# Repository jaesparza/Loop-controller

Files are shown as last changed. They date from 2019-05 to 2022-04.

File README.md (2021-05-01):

# Loop antenna tunning control <br>

> - High voltage and currents can develop in an efficient loop antenna. If not properly constructed, lethal currents could be derived to your control board.  
> - I make no claims with regards to RF safety, EMC compatibility or compliance to standards of any kind.
> - This is a home-made prototype for hobby applications, you (as potential builder) are solely responsible for your actions.

This project implements a tunning control system for magnetic loop antennas. The antenna is tunned by turning a variable capacitor through a stepper motor at reduced speeds. The controller generates the step signals to be provided to the driver, allows movement only within the specified limits and handles the user interface.

Main characteristics:
- Configurable speeds for fast and slow operation.
- Support for stepper motors of different pulses per rotation and with planetary reductions.
- Smooth stepper motor rotation through microstepping.
- Movement limitation based on discrete step counts or on encoder readings via ADC.

This repository hosts:
- Design calculations
- Hardware designs: schematic, PCB layouts and Gerbers ready to upload for production
- Software implementation of a reconfigurable controller to operate vacuum and butterfly capacitors, with different rotation limit control strategies.
- Notes on mechanical aspects and component selection.

The repository hosts two prototypes: a wired and a wireless control system. As of today only the wired system is complete.

## Wired control - Completed and deployed

| [Software](https://github.com/jaesparza/Loop-controller/tree/master/Software/tunerControllerGen1) | 
[Hardware](https://github.com/jaesparza/Loop-controller/tree/master/pcb/initialPrototype) |

This is a working system relying on a wired connection to deliver motor coil currents as well as reading back the encoder position.

The user interface is implemented through:
- a 16x2 LCD screen to display current capacitor position with a bar and a count,
- two push buttons to trigger clockwise or counter-clockwise rotations,
- a switch to select fast or slow speed.

In my implementation I use an ethernet network cable to be run in parallel with the coaxial cable carrying the RF singal. I have not experienced problems with electrical noise or spurious readings in the ADC due to long cable runs.

## Wireless control - Prototype, on hold
Currently under development, this second version of the controller features wireless control over 802.15.4. The remote control board is intended to be placed together with the antenna in the remote location. The user interacts with the control through a PC application.

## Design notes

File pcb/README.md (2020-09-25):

# Hardware notes

Fixes:

* **Pull-up fix in the enable motor stepper controller signal**  it is important to add a 1 kOhm pull-up to the enable signal so it has a defined state when the microcontroller is going through a power-on/reset. It can be added easily on the back of the PCB between the *Enable* and the *Vcc* pins.

## Wired control board
- Only revB of the PCB is available in here, revA had routing problems and was discarded in the design tool.
- The hardware was developed with easyEDA and I used JLPCB for production.

## Wireless control board
- The hardware was developed with KiCAD and I used JLPCB for production.

Misc. notes:
- Power through LiPo battery - solar panel could be used.
- The control board runs at 3V to reduce power consumption and to avoid level shifters to interface peripherals. Software is currently under development.

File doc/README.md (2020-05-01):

# Documentation

## Datasheets
Due to copyright I do not upload datasheets to GitHub, but I do keep a list of links to the original sources so it is easy to find information.
* Stepper motor driver Allegro A4988 - [Link to datasheet](https://www.pololu.com/file/0J450/a4988_DMOS_microstepping_driver_with_translator.pdf)
* Microcontroller ATmega 328p - [Link to datahseet](http://ww1.microchip.com/downloads/en/DeviceDoc/Atmel-7810-Automotive-Microcontrollers-ATmega328P_Datasheet.pdf)
* Microcontroller ATmega32U5 - [Link to datasheet](http://ww1.microchip.com/downloads/en/DeviceDoc/Atmel-7766-8-bit-AVR-ATmega16U4-32U4_Summary.pdf)
* FTDI cable pinout - [Link to manual](https://www.ftdichip.com/Support/Documents/DataSheets/Cables/DS_TTL-232R_CABLES.pdf)
* Stepper motor with planetary reduction 5:1 - 17HS15-1684S-PG5 -[Link to datasheet](https://www.omc-stepperonline.com/download/17HS15-1684S-PG5.pdf)
* Stepper motor 400 rev - 42BYGHM809 - Available in this repository

## Schematics
* Arduino pro mini - Available in this repository - License Attribution Share-Alike 3.0
* Arduino pro micro - Available in this repository - License Attribution Share-Alike 4.0
* A4988 breakout board [Link to schematic](https://a.pololu-files.com/picture/0J3359.600.jpg?bafae85a9d4ff4a7837ec16a322748fe)
* Minimal circuit needed to drive the stepper in a test setup [Link to schematic](https://a.pololu-files.com/picture/0J10073.600.jpg?75d9ca5bb2e095e5c5f64350019e1b81)

## Others
* Mechaduino [hardware](https://github.com/jcchurch13/Mechaduino-Hardware) and [firmware](https://github.com/jcchurch13/Mechaduino-Firmware) git repositories.

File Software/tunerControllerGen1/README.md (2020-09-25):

# Tuner controller - Generation 1
This is the firmare for the first generation control board. It has been developed using CPP and parts of the Arduino framework as Hardware Abstraction Layer (HAL). 

Main features are:
* The firmware can be configured to control different kinds stepper motors at different speeds.
* The LCD position bar can be recalibrated to represent approximate capacitance graphically between min and max values.
* The LCD refresh rate can be reconfigured so it does not affect motor operation.
* Capacitor position is stored in EEPROM and therefore is persistent accross reboots.
* The firmare is easily portable to other architectures by changing the hw dependand class implementations (`Input.cpp`, `StepperMotor.cpp`, `UI.cpp` and `EepromAccess.h`).

## Operation

* Select speed by toggling the speed switch between SLOW or FAST.
* Move the capacitor in the desired direction by pushing CW or CCW. Progress bar and rotation count are incremented during movement and immediately upon pushbutton release.
* To clear EEPROM contents and set the position count to 0:
  1. Push reset button.
  2. Push both CW and CCW buttons at the same time.
  3. Release the reset button while keeping CW and CCW pushed.
  4. Release CW and CCW
  5. Board will boot and set the position to 0.

## Software structure
The control software is structured as depicted below. Comments after `##`

```bash
tunerControlGen1/
|── tunnerControllerGen1.ino                ## Initialization and entry point
├── HardwareConfig.h                        ## Configuration of hardware connections and motor timing
├── src/                                    
│   ├── lib                                 ## Third party library for faster LCD interfacing (no blocking)
|   |   ├── LiquidCrystalFast.h
|   |   └── LiquidCrystalFast.cpp
│   ├── modes                               ## Operational modes
|   |   ├── Mode.h
|   |   ├── ModeCalibrate.h
|   |   └── ModeOperate.h
│   ├── hwControl                           ## Hardware dependant class definitions and implementations for Arduino
|   |   ├── characterDefinitions.h
|   |   ├── UI.h
|   |   ├── UI.cpp
|   |   ├── StepperMotor.h
|   |   ├── StepperMotor.cpp
|   |   ├── EepromAccess.h
|   |   ├── Input.h
|   |   └── Input.cpp
|   └── 
└── 
```

## How to configure the firmware

The firmaware can be configured to drive motors at different speeds by altering the timing parameters in the table below. Additionally, care must be taken so the update of the LCD does not interfere the driver pulsing to a point in which it affects smooth movement. This can be controlled by modifying the number of pulses required to trigger a display update. 

| Parameter name | Description | Unit |
|---| ---|---|
| DELAY_SLOW | Pulse duration for slow operation. | microseconds | 
| DELAY_FAST | Pulse duration for fast operation. | microseconds | 
| OPERATION_DELAY_SLOW  | Delay between pulses in slow mode.| milliseconds |
| OPERATION_DELAY_FAST  | Delay between pulses in fast mode.| milliseconds | 
| DECIMATE | Division factor applied to the steps count printed on the LCD | N/A - discrete count|
| MAX_COUNT | Maximum number of counts for a full progress bar. | steps | 
| REFRESH_INTERVAL | Number of pulses needed to trigger a LCD update. | N/A - discrete count  |
| SOFT_LIMIT_MIN | Minimum stepper count. Steps will not be sent below this limit (CW steps).| steps |
| SOFT_LIMIT_MAX | Maximum stepper count. Steps will not be sent above this limit (CCW steps).| steps|
| ENCODER_MIN || raw adc counts|
| ENCODER_MAX || raw adc counts|

These parameters can be set in the file `HardwareConfig.h` by activating the relevant configuration via `#define CONF_#` or writing an additional one. Extract of HardwareConfig, with `CONF_1` as active configuration below.

```C
#define CONF_1

#ifdef CONF_1
/* Configuration for a stepper motor of 400 pulses per revolution, no planetary
 * reduction built-in.
 *
 *  This motor is intented to be used with a butterfly capacitor. This capacitor
 * type goes from minimum capacity to maximum with a 90 deg rotation = 1/4 of a
 * full rotation. Coupling to the capacitor is directly to the shaft (no
 * additional mechanical reduction).
 *
 *  Microswitches configured for maximum microstepping for minimum vibrations.
 *  switches 1 - LOW
 *           2 - LOW
 *           3 - LOW
 */
#define REFRESH_INTERVAL     50
#define DELAY_SLOW           300
#define DELAY_FAST           100
#define MAX_COUNT            1600
#define DECIMATE             1
#define OPERATION_DELAY_SLOW 50
#define OPERATION_DELAY_FAST 10
#define SOFT_LIMIT_MIN       0
#define SOFT_LIMIT_MAX       1600
#endif // CONF_1
```

In addition to the parameters from above, microstepping in the stepper driver is recommended for smoother operation. This firmware interfaces the A4988 driver, that supports the following microstepping options:

| MS1 | MS2 | MS3 | Microstep |
|-----|-----|-----|---|
| L | L | L | Full step |
| H | L | L | 1/2  step |
| L | H | L | 1/4 step  |
| H | H | L | 1/8 step  |
| H | H | H | 1/16 step |

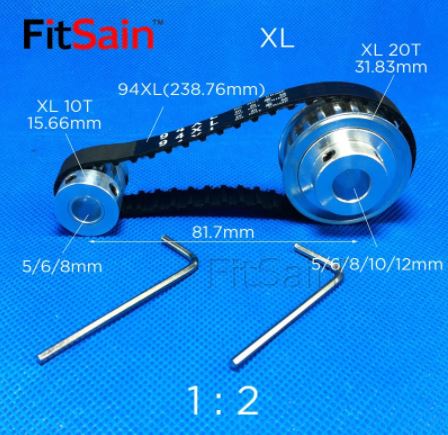
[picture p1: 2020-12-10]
doc/images/tansmission.JPG

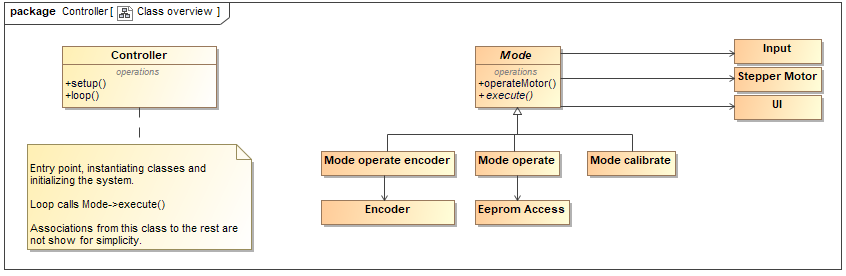
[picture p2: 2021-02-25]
doc/images/controllerStructure.PNG

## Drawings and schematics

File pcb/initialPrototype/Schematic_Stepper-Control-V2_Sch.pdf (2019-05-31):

## VCC VCC

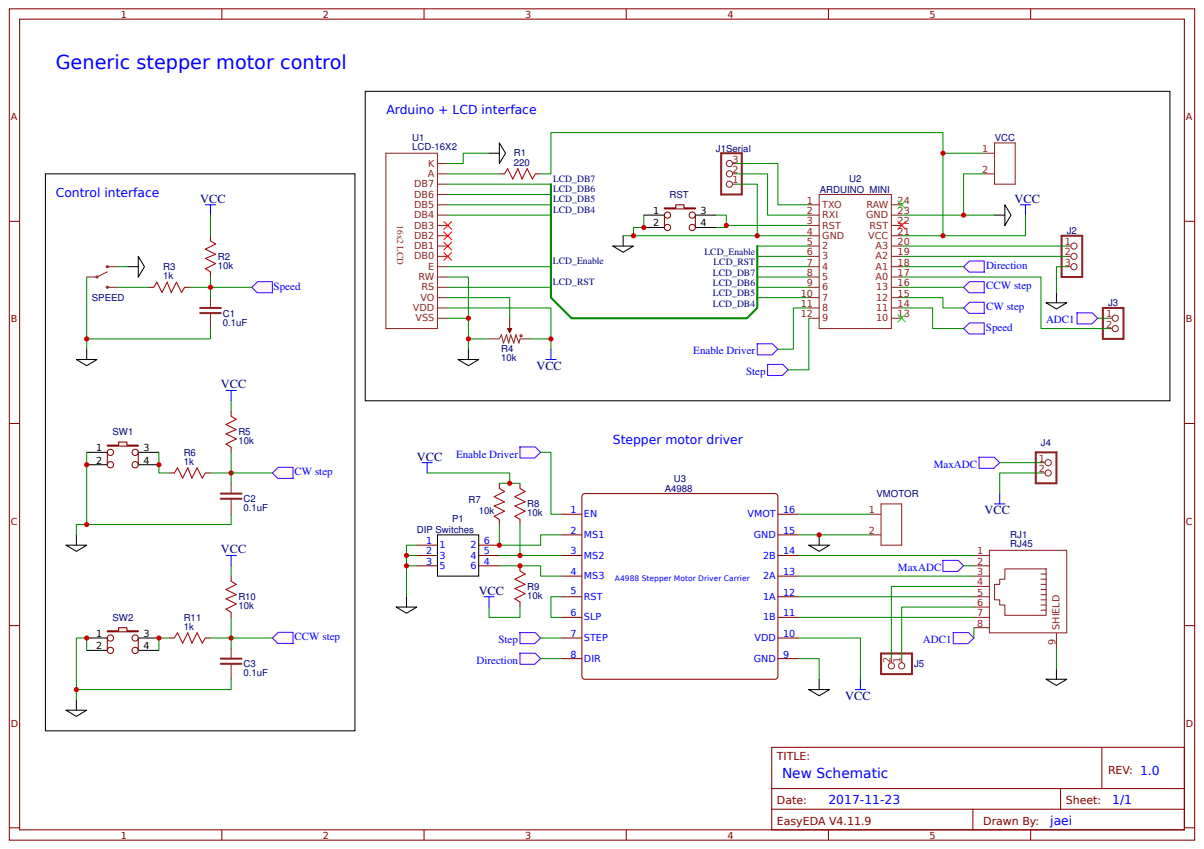
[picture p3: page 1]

Generic stepper motor control

A4988 Stepper Motor Driver Carrier

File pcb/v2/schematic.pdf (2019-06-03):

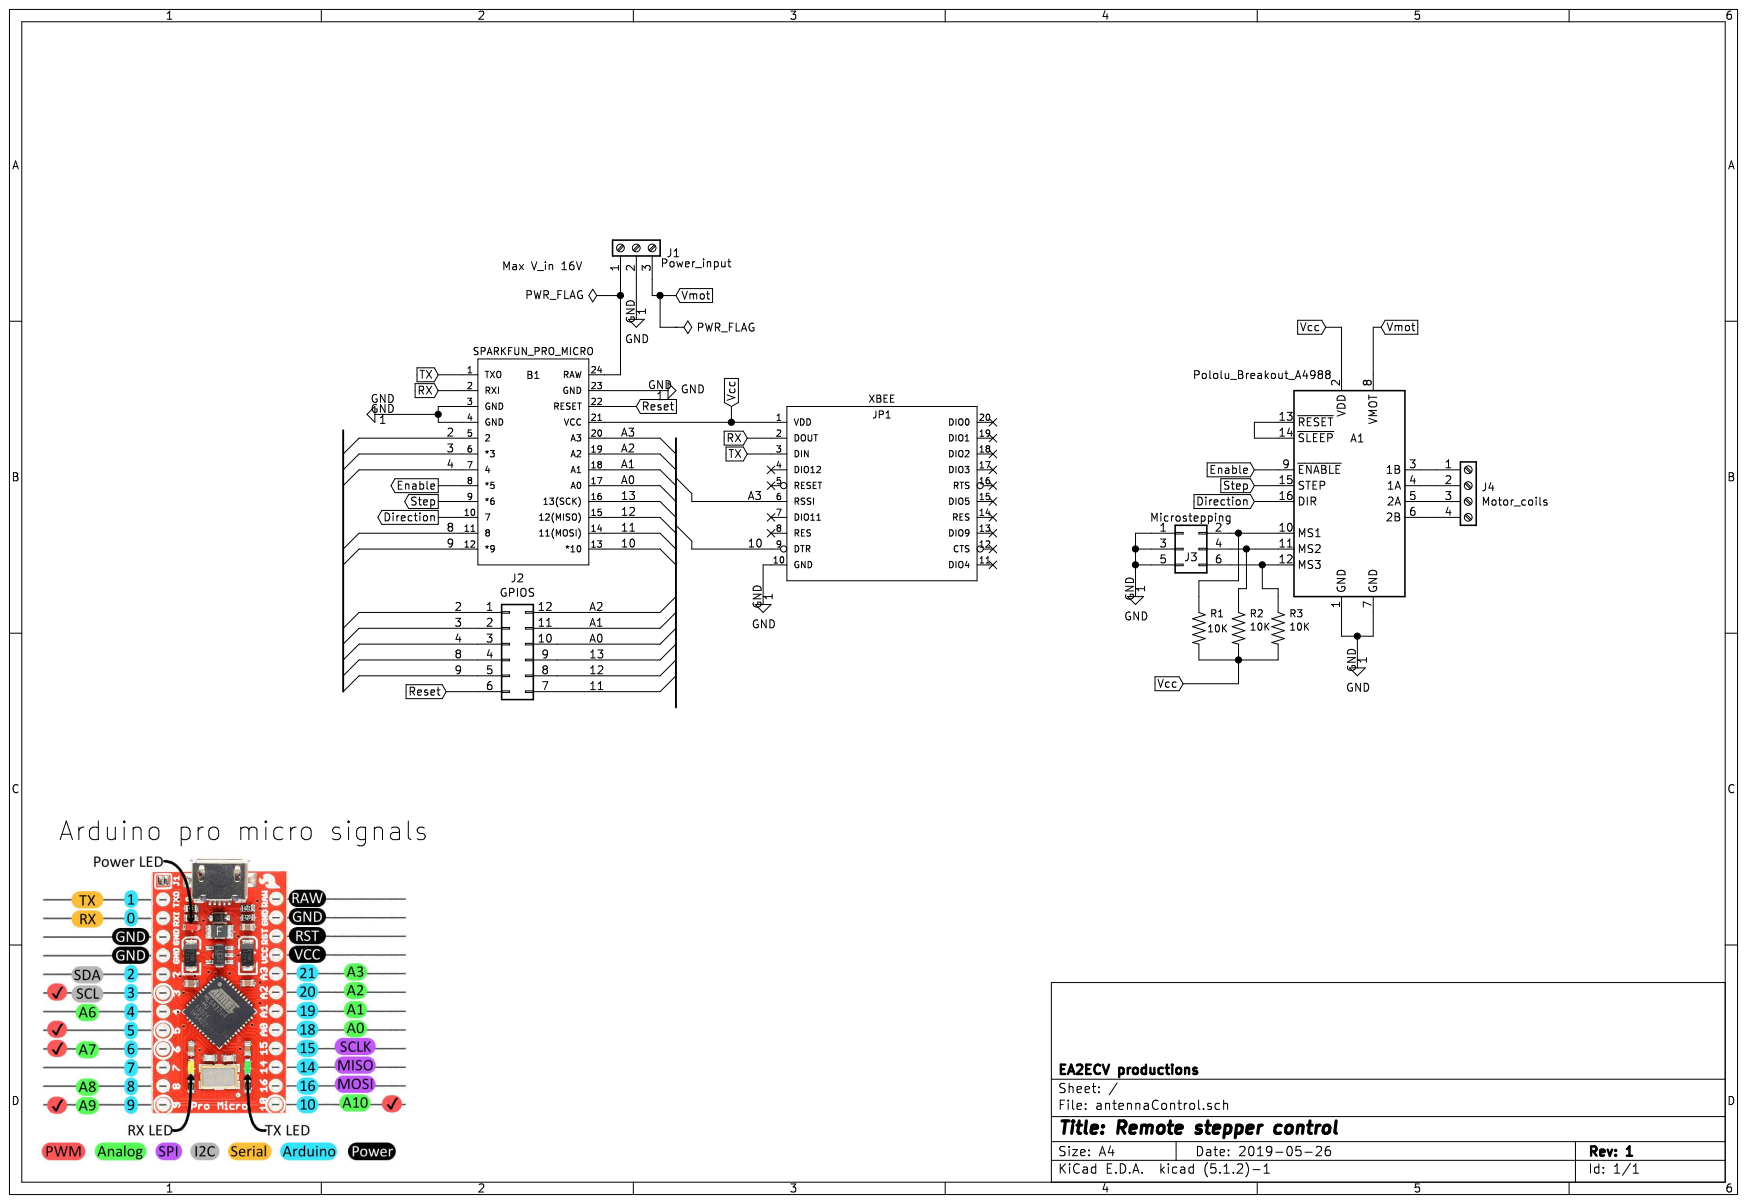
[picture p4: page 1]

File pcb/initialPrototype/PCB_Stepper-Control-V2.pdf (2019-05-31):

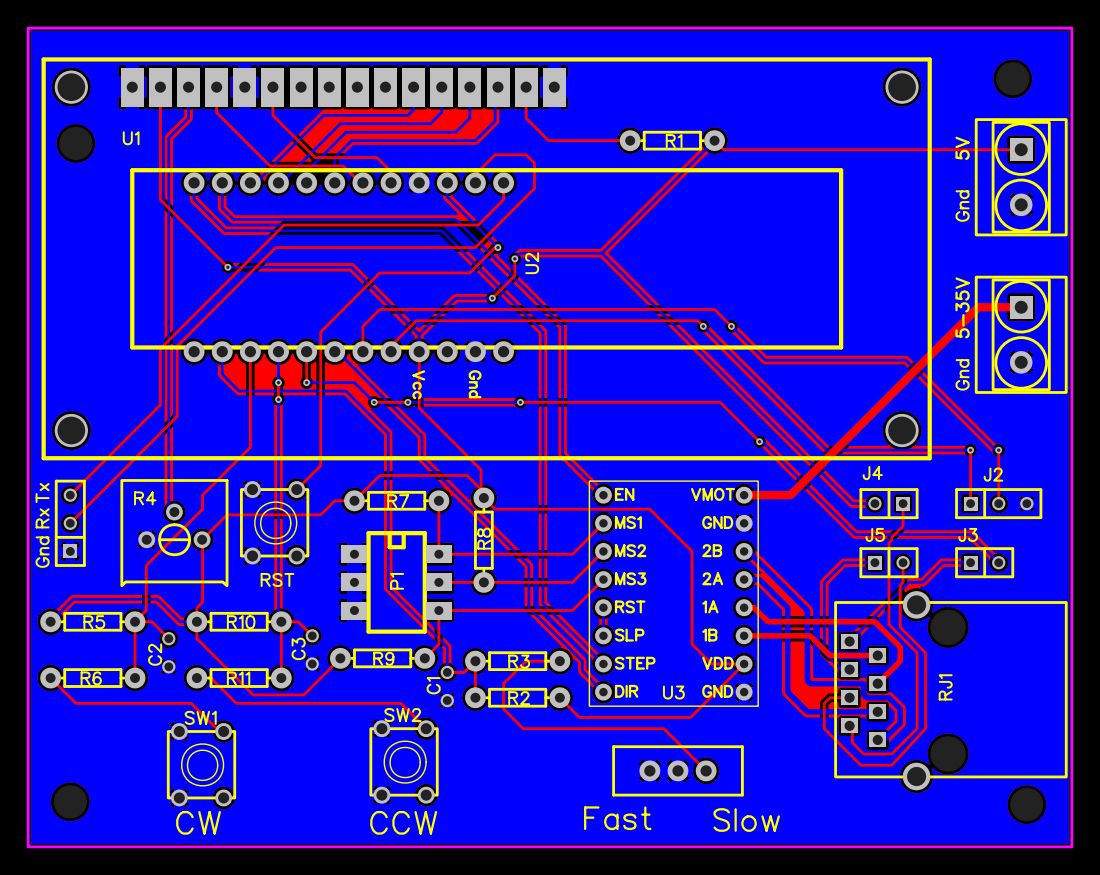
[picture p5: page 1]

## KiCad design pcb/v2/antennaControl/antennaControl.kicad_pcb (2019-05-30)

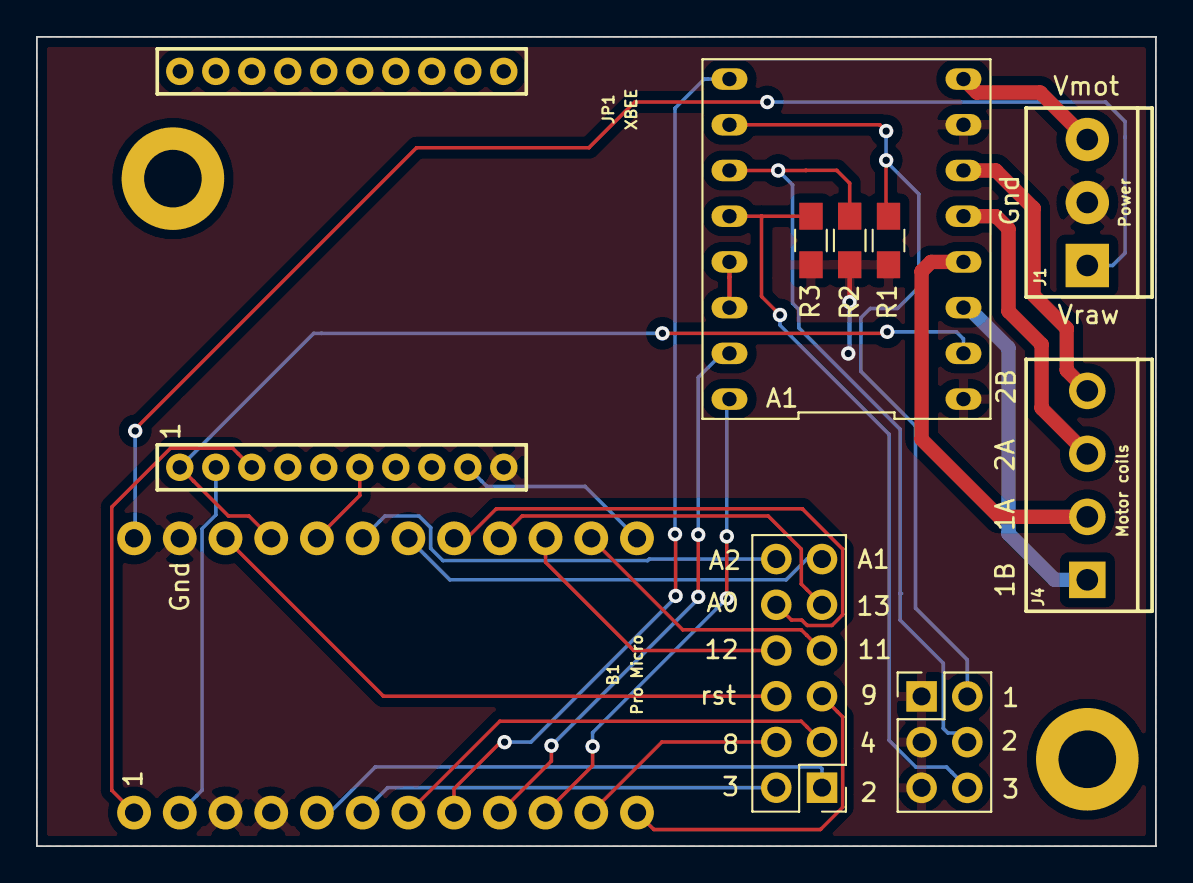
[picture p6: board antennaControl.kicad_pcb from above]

Board: 2 copper layers, 62.2 x 45.0 mm, 12 parts (0 on the bottom side), 31 nets.

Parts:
A1: Breakout_A4988; Pololu_Breakout_4988
B1: Pro Micro; SPARKFUN_PRO_MICRO
J1: Power; SCREWTERMINAL-3.5MM-3
J2: GPIOS; Pin_Header_Straight_2x06_Pitch2.54mm
J3: Microstepping; Pin_Header_Straight_2x03_Pitch2.54mm
J4: Motor coils; SCREWTERMINAL-3.5MM-4
JP1: XBEE
R1, R2, R3: 10K; R_0805_HandSoldering
REF1: M3_2; MountingHole_3.2mm_M3_ISO7380_Pad
REF2: M3_1; MountingHole_3.2mm_M3_ISO7380_Pad

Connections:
/2: B1.5, J2.1
/3: B1.6, J2.2
/4: B1.7, J2.3
/8: B1.11, J2.4
/9: B1.12, J2.5
/10: B1.13, JP1.9
/11: B1.14, J2.7
/12: B1.15, J2.8
/13: B1.16, J2.9
/A0: B1.17, J2.10
/A1: B1.18, J2.11
/A2: B1.19, J2.12
/A3: B1.20, JP1.6
Direction: A1.16, B1.10
Enable: A1.9, B1.8
GND: A1.1, A1.7, B1.3, B1.4, B1.23, J1.2, J3.1, J3.3, J3.5, JP1.10, R1.2, R2.2, R3.2
unnamed: A1.3, J4.1
unnamed: A1.4, J4.2
unnamed: A1.5, J4.3
unnamed: A1.6, J4.4
unnamed: A1.10, J3.2, R1.1
unnamed: A1.11, J3.4, R2.1
unnamed: A1.12, J3.6, R3.1
unnamed: A1.13, A1.14
unnamed: B1.24, J1.1
RX: B1.2, JP1.2
Reset: B1.22, J2.6
Step: A1.15, B1.9
TX: B1.1, JP1.3
Vcc: A1.2, B1.21, JP1.1
Vmot: A1.8, J1.3

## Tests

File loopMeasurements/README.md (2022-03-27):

# S11 measurements of the loop antenna

Measurements of the S11 parameters the loop antenna build. Conducted with a NanoVNA and exported using NanoVNAQt. 

An example measurement can be seen below. The screenshot is taken directly on the NanoVNA and it shows the antenna permance in the 20m band.

<center>
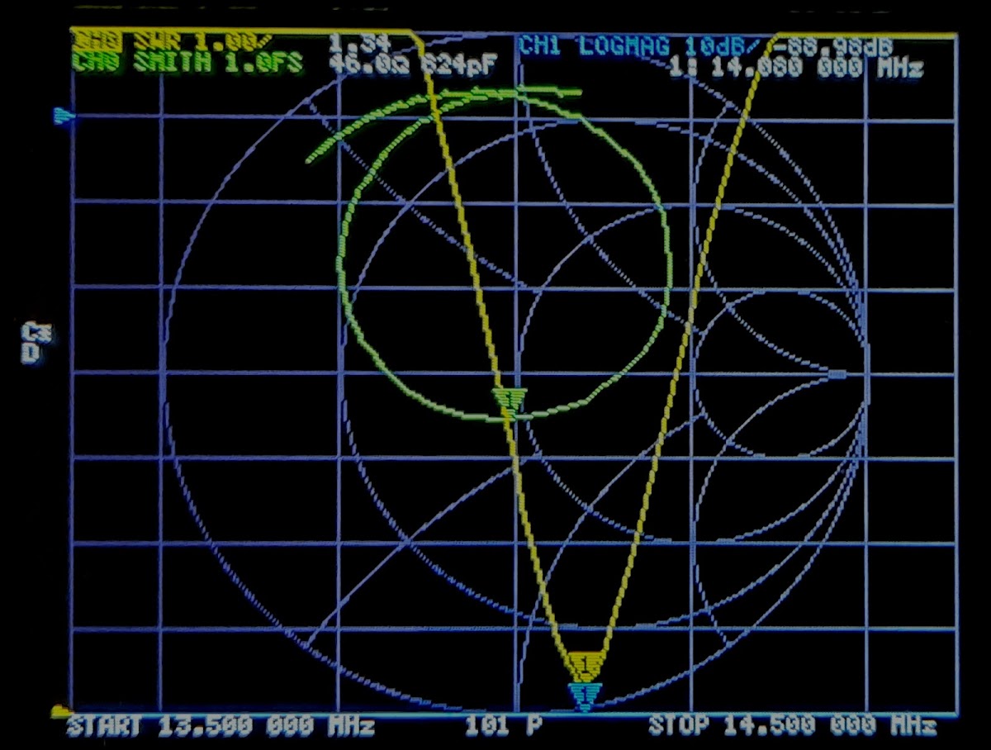
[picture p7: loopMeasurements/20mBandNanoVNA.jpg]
SWR20mband

</center>

## Description of the content
* Plotting: scripts used to plot the readings stored in the touchstone files.
* Office Location March 22: accurate measurements conducted with a calibrated device.
* Device uncalibrated: old measurements with uncalibrated device. Do not use.

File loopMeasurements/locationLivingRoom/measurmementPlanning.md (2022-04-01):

## Planning the measurements

Conducting measurements:
* [X] For each range to measure, calibrate the device.
* [X] For each band measurements one file: bandNameDate.
* Guideline: Measure in steps of 1kHz (at least)
* Date in format DayMonthYear in two digit format: e.g. 20m120222 for 20m band measured on the 12 of Feb year 2022

Perform measurments for the following bands:

### 20m | 14MHz
* 14.000 - Measurement center, span 700 kHz, 500 points
* 14.175
* 14.350

bandwidth 350 kHz

[X] Measurements in file 20m310322

### 17m | 18 MHz
* 18.068
* 18.118 Measure
* 18.168

bandwidth 100 kHz

[X] Measurements in file 17m260322

### 15m | 21 MHz
* 21.000
* 21.225 Measure
* 21.450

bandwidth 450 kHz

Sweep in  segments,  Hz/step

### 12m | 24 MHz
* 24.890
* 24.940 Measure
* 24.990

bandwidth 100 kHz

[X] Measurements in file 12m310322

### 10m | 28 MHz
* 28.000
* 29.700 - Measure the highest usable frequency of the band

bandwidth 1700 kHz

[X] Measurements in file 10m260322

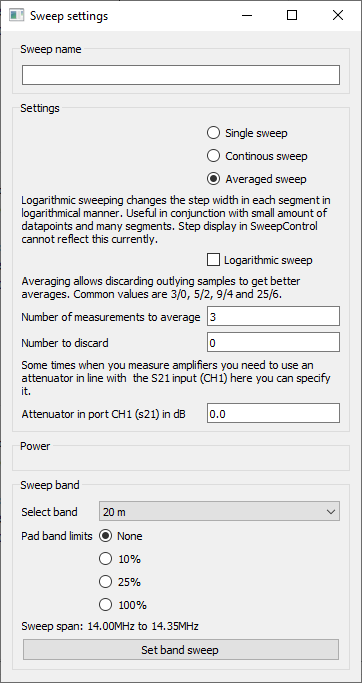
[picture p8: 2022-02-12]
loopMeasurements/deviceUncalibrated/snapshots/averageConfiguration.PNG

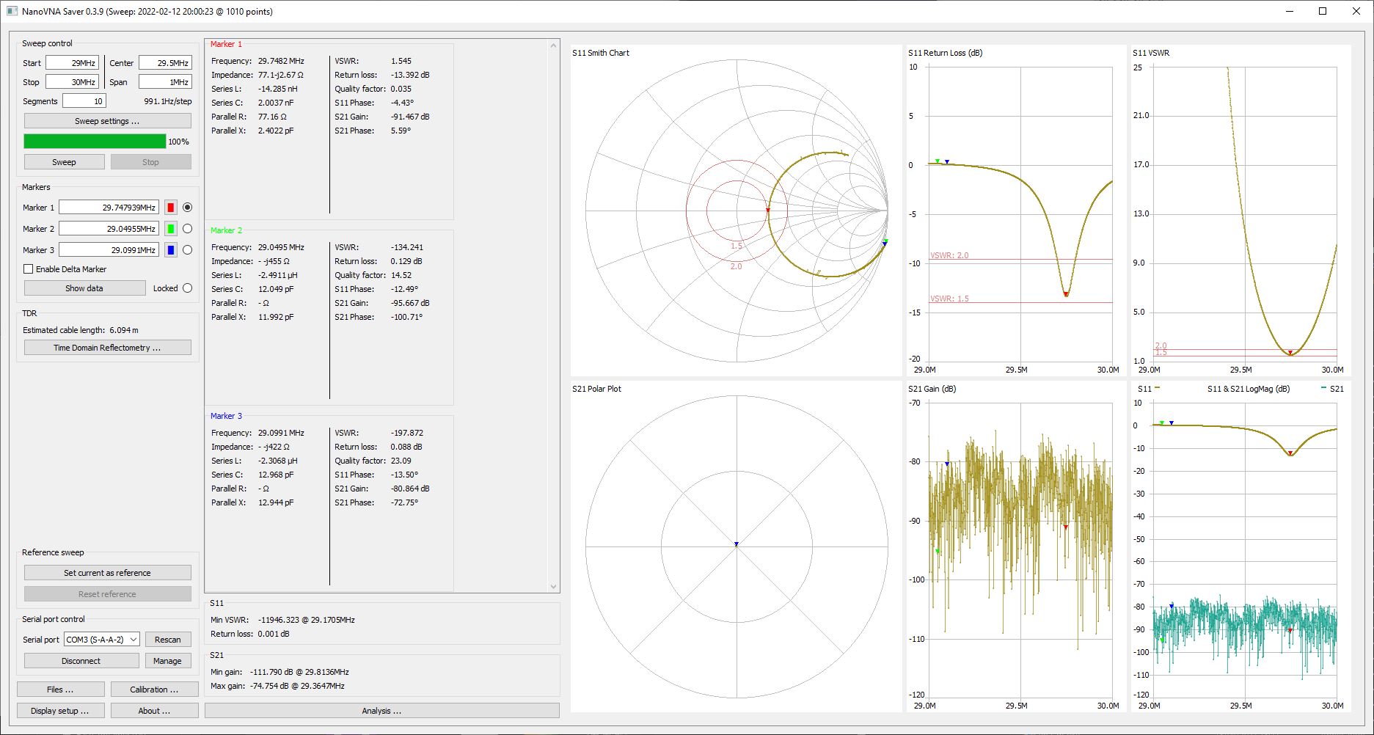
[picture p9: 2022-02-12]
loopMeasurements/deviceUncalibrated/snapshots/10m.PNG

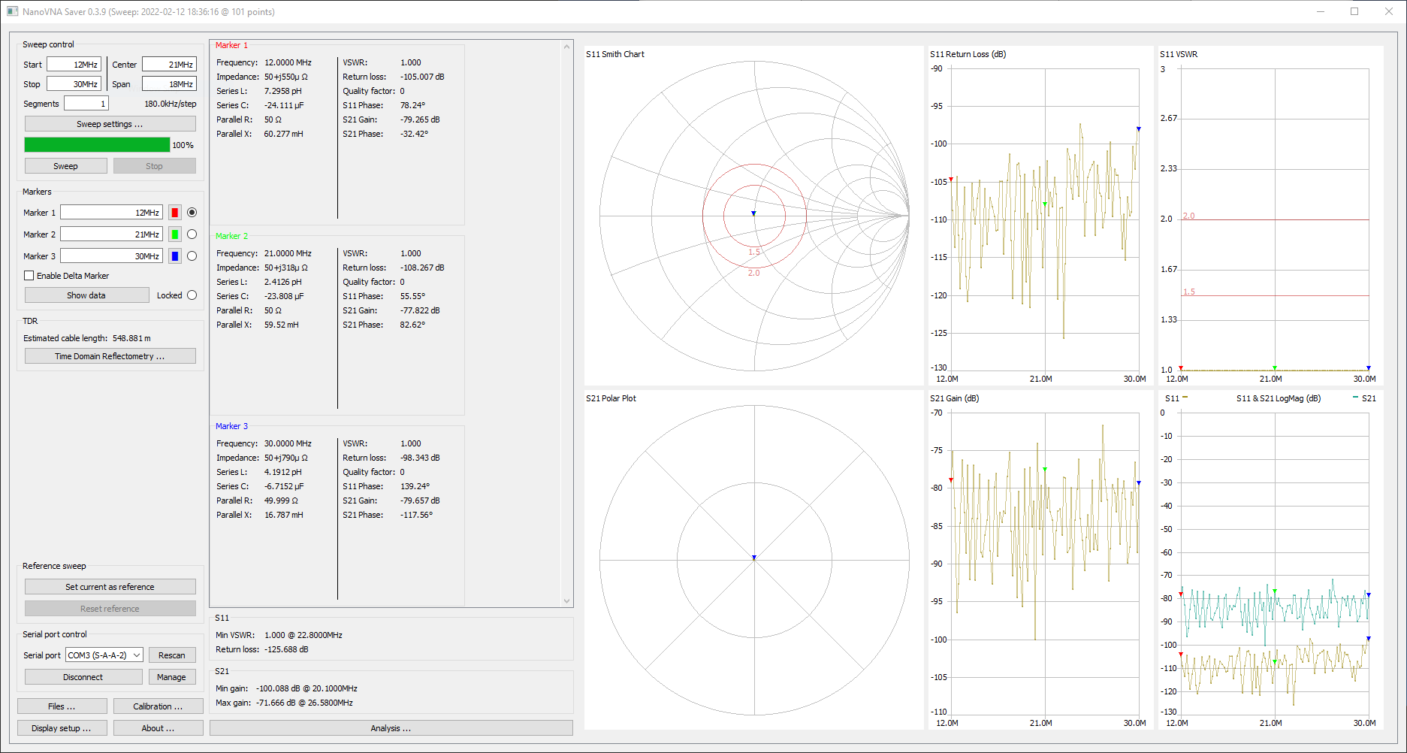
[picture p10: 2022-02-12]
loopMeasurements/deviceUncalibrated/snapshots/afterCalibration.PNG

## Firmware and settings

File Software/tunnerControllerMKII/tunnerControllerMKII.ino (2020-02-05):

/* 
 * Project: Remote controller v2
 * Author: ja - jaesparza@gmail.com
 * Description: Remote control of a stepper motor.
*/

#include <stdlib.h>
#include <string.h>

#include "hardwareConfiguration.h"

const int bSize = 50;

// Motor control definitions
#define MOTOR_ENABLE    LOW
#define MOTOR_DISABLE   HIGH
#define SLOW            1
#define FAST            0

#define XBEE_ON         LOW
#define XBEE_OFF        HIGH

#define CCW             HIGH
#define CW              LOW

char Buffer[bSize];  // Serial buffer
char Command[10];    // Arbitrary Value for command size
char Data[15];       // ditto for data size
int ByteCount;
bool fastMode = false;


int ret = 0;
char * cmd = "a";
   
void SerialParser(void) {
//
//  One command per line.  Eventually, Data may have multiple 
//   fields separated by ":"
//  Command Format: "up to 5 Letter command, up to 10 letter data<\n>"
//                  No checking.
//
//  count will  be below Zero on a timeout.
//  read up to X chars or until EOT - in this case "\n" 
   ByteCount = -1;
   ByteCount =  SERIAL.readBytesUntil('\n',Buffer,bSize);  
    
   if (ByteCount  > 0) {
        strcpy(Command,strtok(Buffer,","));
                   
        strcpy(Data,strtok(NULL,","));     
   }
   memset(Buffer, 0, sizeof(Buffer));   // Clear contents of Buffer
   SERIAL.flush();
}

void clearBuffer() {
    strcpy(Command,"");
}

void disableStepper()
{
  digitalWrite(ENABLE_PIN, MOTOR_DISABLE); 
}

void enableStepper()
{
  digitalWrite(ENABLE_PIN, MOTOR_ENABLE);
}

void setup()
{
  // Set the pin direction for the peripherals
  // Pin direction for motor control signals
  pinMode(ENABLE_PIN,     OUTPUT);
  pinMode(STEP_PIN,       OUTPUT);
  pinMode(DIRECTION_PIN,  OUTPUT);
  pinMode(MS1_PIN,        OUTPUT);
  pinMode(MS2_PIN,        OUTPUT);
  pinMode(MS3_PIN,        OUTPUT);
  
  // Pin direction for RX led
  pinMode(RXLED,      OUTPUT);
  // Pin direction for sleep pin in XBee
  pinMode(SLEEP_PIN,  OUTPUT);

  digitalWrite(MS1_PIN,HIGH);
  digitalWrite(MS2_PIN,HIGH);
  digitalWrite(MS3_PIN,HIGH);

  pinMode(DEBUG_1, OUTPUT);
  pinMode(DEBUG_2, OUTPUT);
  digitalWrite(DEBUG_1, LOW);   

  //digitalWrite(SLEEP_PIN,XBEE_OFF);
  enableStepper();

  digitalWrite(DIRECTION_PIN, CW);

  // Initialize serial ports
  Serial1.begin(9600); // Serial through exposed RX/TX, hardware UART
                       // Attached to XBee, 
  
  // Serial over USB (Serial Monitor) -- Do not use while powered externally!
   Serial.begin(9600);
   Serial.println("Loop initialized");
}

void customStep(const int motorDelay)
{
  digitalWrite(STEP_PIN,LOW);
  delay(motorDelay);
  digitalWrite(STEP_PIN,HIGH);
  delay(motorDelay); 
}

void step() 
{
  digitalWrite(STEP_PIN,LOW);
  if (fastMode) 
  {
     delay(1); 
  }
  else 
  {
    delay(10);
  }
  digitalWrite(STEP_PIN,HIGH);
  if (fastMode)
  {
    delay(1); 
  }
  else 
  {
    delay(10);
  }
}
void ledToggle()
{
  digitalWrite(RXLED, LOW);   // set the RX LED ON
  digitalWrite(RXLED, HIGH);    // set the RX LED OFF
}

byte stateWord = 0;
char stateWord2 = 0;

bool done = false;

const int bufferSize = 10;

char buffer[bufferSize];

void clearBuffer(char * buf,int bufSize){
  for(int i =0; i<bufSize; i++) {
    buffer[i] = 0;
  }
}


void loop()
{
digitalWrite(DEBUG_2, LOW); 
    SerialParser();

    switch (Command[0]) {
      case 's':
        //SERIAL.println("Slow");
        //step(100);
        fastMode = false;
        break;
      case 'f':
        //SERIAL.println("Fast");
        //step(10);
        fastMode = true;
        break;
      case 'w': // CCW mode
        digitalWrite(DIRECTION_PIN, CCW);
        step();
        //step(atoi(Data));
        break;
      case 'c':
        digitalWrite(DIRECTION_PIN, CW);
        step();
      default:
        break;
    }
    
    clearBuffer();
    digitalWrite(DEBUG_2, HIGH); 
  
}

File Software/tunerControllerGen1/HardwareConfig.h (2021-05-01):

/*
 *  Filename: HardwareConfig.h
 *
 * Description:
 *  - Contains the hardware specific configurations
 *  - Defines timing delays for stepper motor control
 *
 * This software can be reused with other hardware configuration by only
 * changing the signal mapping.
 *
 * WARGING: High voltages and lethal currents can develop in an efficient loop
 * antenna. If not properly constructed, lethal voltages could be derived to
 * your control board. Us it at your OWN risk.
 *
 * Last update: see GIT log
 *
 * Author: jaesparza - jaesparza@gmail.com
 */

#ifndef HARDWARECONFIG_H_
#define HARDWARECONFIG_H_

/////////// REMAP AT YOUR OWN RISK   ///////////////////////////////

// User Input/Output signals
#define CCW_IN      13
#define CW_IN       12
#define SPEED       11
#define BUTTON_1_IN A3

#define PROFILE_PIN A2

// Potentiometer connected to ADC channel 0
#define ENCODER A0

// Stepper driver signals
#define STEP_PIN      9
#define ENABLE_PIN    8
#define DIRECTION_PIN A1

// LCD signals
#define RS     3
#define ENABLE 2
#define D4     7
#define D5     6
#define D6     5
#define D7     4
/////////////////////////////////////////////////////////////////////

// LCD interface definitions
#define COLUMNS       16
#define ROWS          2
#define COUNT_PER_COL (MAX_COUNT / COLUMNS)

// Select the configuration to be used
#define CONF_3

#ifdef CONF_1
/* Configuration for a stepper motor of 400 pulses per revolution, no planetary
 * reduction built-in.
 *
 *  This motor is intented to be used with a butterfly capacitor. This capacitor
 * type goes from minimum capacity to maximum with a 90 deg rotation = 1/4 of a
 * full rotation. Coupling to the capacitor is directly to the shaft (no
 * additional mechanical reduction).
 *
 *  Microswitches configured for maximum microstepping for minimum vibrations.
 *  switches 1 - LOW
 *           2 - LOW
 *           3 - LOW
 */
#define REFRESH_INTERVAL     50
#define DELAY_SLOW           300
#define DELAY_FAST           100
#define MAX_COUNT            1600
#define DECIMATE             1
#define OPERATION_DELAY_SLOW 50
#define OPERATION_DELAY_FAST 10
#define SOFT_LIMIT_MIN       0
#define SOFT_LIMIT_MAX       1600
#endif // CONF_1

#ifdef CONF_2
/*  Configuration for a stepper motor 200 pulses per revolution and
 *  a planetary gear reduction of 1:5
 *
 *  This motor is intented to be used with a vacuum capacitor of 16 turns and
 * coupled directly to the capacitor shaft (no additional mechanical reduction).
 *
 *  Microswitches configured for maximum microstepping for minimum vibrations.
 *  switches 1 - LOW
 *           2 - LOW
 *           3 - LOW
 */
#define REFRESH_INTERVAL     3000
#define DELAY_SLOW           300
#define DELAY_FAST           150
#define MAX_COUNT            15900
#define DECIMATE             10
#define OPERATION_DELAY_SLOW 0
#define OPERATION_DELAY_FAST 0
#define SOFT_LIMIT_MIN       0
#warning "Soft limit max remains to be checked"
#define SOFT_LIMIT_MAX 15900000

#endif

#ifdef CONF_3
/*  Configuration for a stepper motor 200 pulses per revolution and
 *  a planetary gear reduction of 1:5
 *
 *  This motor is intented to be used with a vacuum capacitor of 16 turns and
 *  coupled directly to the capacitor shaft (no additional mechanical
 * reduction).
 *
 *  Microswitches configured for maximum microstepping for minimum vibrations.
 *  switches 1 - LOW
 *           2 - LOW
 *           3 - LOW
 */

#define REFRESH_INTERVAL     3000
#define DELAY_SLOW           300
#define DELAY_FAST           150
#define MAX_COUNT            15900
#define DECIMATE             1
#define OPERATION_DELAY_SLOW 0
#define OPERATION_DELAY_FAST 0

#define ENCODER_MIN 350 //(before 378)
#define ENCODER_MAX 1020

#define ADC_COUNTS_PER_COL 42 // ((ENCODER_MAX - ENCODER_MIN) / 16)

#endif

#endif /* HARDWARECONFIG_H_ */

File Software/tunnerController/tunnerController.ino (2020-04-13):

#include <Arduino.h>
#include "HardwareConfig.h"
#include "UI.h"

#define MOTOR_ENABLE 0
#define MOTOR_DISABLE 1
#define SLOW 	1
#define FAST 	0

#define PUSHED   0
#define RELEASED 1

boolean cMode = false;
boolean calibrationComplete = false;

volatile long rotationCount = 0;

int speedIn = 0;
int cwIn = 0;
int ccwIn = 0;
int extraPB = 0;

int lastRefresh = 0;

void setup() {

  // Initialize hardware
  initLCD();
  initIO();
  initMotorState();
  initSerial();

  // Initialize UI
  // makeFullBar();
  // makeEmptyBar(1,16);

  showText();

  delay(400);

  // Check inputs and enter configuration configuration mode if requested
  readInputs();
  if (extraPB==PUSHED) {
    cMode = true;
  }

  // Some demo code to test the progress bar
  for(int i= 0; i<16;i++) {
   updateScreen(i);
   delay(50);
  }
  for(int i= 15; i>=0;i--) {
   updateScreen(i);
   delay(50);
  }

}

bool storeMaxCount(int maxCount) {

  return true;
}

void sendPulse(int orientation) {

    int duration = 0;
    if (speedIn == SLOW) {
       duration = DELAY_SLOW;
       if (orientation ==ROTATE_CW){
          rotationCount = rotationCount + 1;
       }
       else {
         rotationCount = rotationCount - 1;
       }
    }
    else
    {
       duration = DELAY_FAST;
       if (orientation ==ROTATE_CW){
          rotationCount = rotationCount + 1;
       }
       else {
         rotationCount = rotationCount - 1;
       }
    }
    digitalWrite(STEP_PIN,HIGH);
    delay(duration);
    digitalWrite(STEP_PIN,LOW);
    delay(duration);
}

void readInputs(){
  speedIn = digitalRead(SPEED);
  cwIn =    digitalRead(CW_IN);
  ccwIn =   digitalRead(CCW_IN);
  extraPB = digitalRead(BUTTON_1_IN);
}


void loop() {
  // set the cursor to column 0, line 1
  // (note: line 1 is the second row, since counting begins with 0):

    if (cMode == true) {
      while(1) { configuration(); } // No need to re-evaluate cMode
    }
    else {
      while(1) { 
        normalOperation(); 
        lastRefresh++;
        //updateScreen(1);
       } // No need to re-evaluate cMode
    }
}

void configuration() {
  //lcd.clear(); // This has to be executed once...
  //lcd.setCursor(0,0);
  //lcd.print(CONFIG_MESSAGE);
   // ask to release button and wait for that
   // to happen
  waitForRelease();
  readInputs();
  if (extraPB == false) { 

    storeMaxCount(10); 
  }
}

boolean waitForRelease(){
  extraPB = digitalRead(BUTTON_1_IN);
  while(extraPB == LOW) {
      extraPB = digitalRead(BUTTON_1_IN);
  }
  return true;
}

void normalOperation() {

  readInputs();
  updateCount(rotationCount);
  updateScreen(rotationCount/COUNT_PER_COL);
  operateMotor();
}

void operateMotor() {
  if ((cwIn == 1) && (ccwIn ==0)) {
      digitalWrite(ENABLE_PIN, MOTOR_ENABLE);
      digitalWrite(DIRECTION_PIN,HIGH);
      sendPulse(ROTATE_CW);
      clearLCDLine(2);
  }
  else if ((ccwIn == 1)&& (cwIn ==0)) {
      digitalWrite(DIRECTION_PIN,LOW);
      digitalWrite(ENABLE_PIN, MOTOR_ENABLE);
      sendPulse(ROTATE_CCW);
      clearLCDLine(2);
  }
  else {
    digitalWrite(ENABLE_PIN, MOTOR_DISABLE);
  }
}

void initIO() {
  pinMode(CW_IN, INPUT);
  pinMode(CCW_IN, INPUT);
  pinMode(SPEED, INPUT);
  pinMode(BUTTON_1_IN,INPUT);
  digitalWrite(BUTTON_1_IN, HIGH); // Enable the internal pull-ups

  pinMode(STEP_PIN,OUTPUT);
  pinMode(ENABLE_PIN,OUTPUT);
  pinMode(DIRECTION_PIN,OUTPUT);
}

void initMotorState() {
  digitalWrite(DIRECTION_PIN,HIGH);
}

void initSerial(){
  Serial.begin(9600);
  Serial.println("Motor driver initialized");
}

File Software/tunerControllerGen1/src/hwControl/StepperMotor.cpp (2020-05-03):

#include "StepperMotor.h"
#include <Arduino.h>

void StepperMotor::initMotorState() {
    disableMotor();
    // digitalWrite(DIRECTION_PIN, HIGH);
}

long StepperMotor::getRotationCount() {
    return rotationCount;
}

void StepperMotor::setSpeed(int speed) {
    if (speed == SLOW) {
        activeDuration = durationSlow;
    } else {
        activeDuration = durationFast;
    }
}

void StepperMotor::rotateCW() {
    digitalWrite(DIRECTION_PIN, HIGH);
    rotationCount--;
    sendPulse();
}

void StepperMotor::rotateCCW() {
    digitalWrite(DIRECTION_PIN, LOW);
    rotationCount++;
    sendPulse();
}

void StepperMotor::enableMotor() {
    digitalWrite(ENABLE_PIN, MOTOR_ENABLE);
}

void StepperMotor::disableMotor() {
    digitalWrite(ENABLE_PIN, MOTOR_DISABLE);
}

void StepperMotor::sendPulse() {
    digitalWrite(STEP_PIN, HIGH);
    delayMicroseconds(activeDuration);
    digitalWrite(STEP_PIN, LOW);
    delayMicroseconds(activeDuration);
}

StepperMotor *StepperMotor::getInstance() {
    if (!instance) {
        instance = new StepperMotor();
    }
    return instance;
}

void StepperMotor::setRotationCount(int rotCount) {
    rotationCount = (long)rotCount;
}

StepperMotor::StepperMotor() {}

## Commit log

2019-05-30 Control board v2
    Control board v2 revA
    [antennaControl.kicad_pcb, antennaControl.sch]
2019-05-30 Added gerbers
    [antennaControl-B_Cu.gbr, antennaControl-B_SilkS.gbr, antennaControl-Edge_Cuts.gbr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]
2019-05-31 Regenerated production files
    Regenerated production files since I was missing soldering mask layers
    [antennaControl-B_Cu.gbr, antennaControl-B_Mask.gbr, antennaControl-B_SilkS.gbr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]
2019-05-31 Added initial prototype design and production files
    [Gerber_BoardOutline.GKO, Gerber_BottomLayer.GBL, Gerber_BottomSilkLayer.GBO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]
2019-06-03 Added exported schematic to pdf
2020-02-05 Create tunnerControllerMKII.ino
    Initial hack to get the motor moving remotely.
2020-04-13 LCD code refactored and progress bar added
    Tested with a 400 steps motor
2020-04-13 Added two configurations, fixed a rev counting bug
    [HardwareConfig.h, tunnerController.ino]
2020-04-27 Added refactored tunnerController for v1 PCB
2020-04-29 Replaced byte type with uint8_t
    [characterDefinitions.h]
2020-04-29 Added Singletos for StepperMotor and UI classes
2020-04-29 Scope resolution and typo fix
    [StepperMotor.cpp, tunerControllerGen1.ino]
2020-04-29 Replaced showMode with showText
    [UI.cpp, UI.h, tunerControllerGen1.ino]
2020-04-29 New movement parameters for the 400 steps motor
2020-04-30 Deprecated initial prototype
2020-04-30 Corrected immediate update functionality to count steps correctly
    [StepperMotor.cpp, StepperMotor.h, UI.cpp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]
2020-04-30 Added storage of capacitor position in NVRAM
2020-04-30 Corrected detection of pushbutton press
    [Input.cpp, tunerControllerGen1.ino]
2020-05-01 Added new temporal configuration for the vacuum capacitor assembly
2020-05-03 Extended the number of counts and added DECIMATE option
    This allows to operate motors with large reductions and still keep track of a maximum number of steps while. DECIMATE allows to divide the total count to create an approximate position representation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
2020-05-09 Added formulas to calculate AC resistance
2020-05-09 Added misc equations and calcuation of the ditributed capacitance
2020-05-18 Added softlimits to the stepper motor movement.
2020-09-20 Added ADC definition and file
2020-09-20 Include ADC and calibration routine using it
2020-09-20 Calibrate mods
2020-09-21 Renamed ADC.h to Encoder.h
2020-09-22 Added new hardware configuration, renamed ADC input
2020-09-22 Refactored operate motor method
2020-09-25 Added compilation switches for difference configurations
2020-10-09 Added the RJ45 breakout board
    [etherBreakout.kicad_pcb, etherBreakout.sch]
2021-04-15 Create arduino.json
    VS code configuration to compile and upload to arduino board pro micro
2021-05-01 Added functionality to update position bar according to encoder readings

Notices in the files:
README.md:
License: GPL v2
